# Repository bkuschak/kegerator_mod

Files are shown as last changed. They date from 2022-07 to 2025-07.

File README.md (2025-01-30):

# kegerator mod  

This project is a workaround to prevent short cycling on the Komos V2 kegerator. 

For some unknown reason the temperature controller occassionally turns the 
compressor on for about 1 second then immediately shuts it off. On my kegerator,
this can happen several times per hour. It tends to happen more often when the 
temperature setpoint is above 45 °F.

The workaround is to insert a small microcontroller board between the controlller
board and the compressor. This board intercepts the signal that controls the 
compressor. The software filters out any short transients and enforces a minimum 
on-time and a minimum off-time for the compressor.  

It has been running fine on my kegerator for several years now.

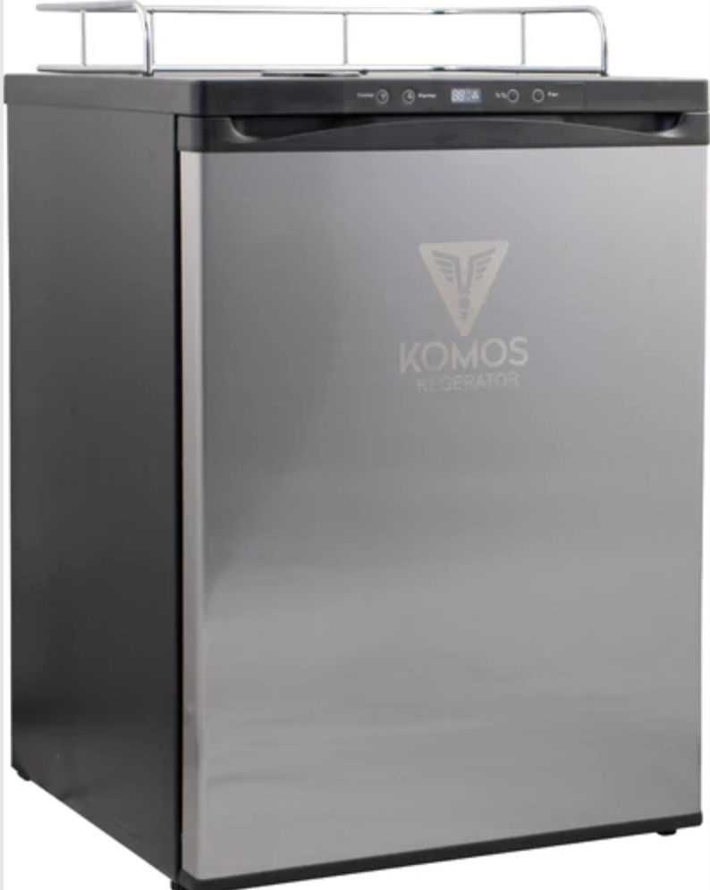
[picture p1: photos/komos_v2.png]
komos_v2


The board is installed inline between the front panel temperature controller and the 
compressor power board.

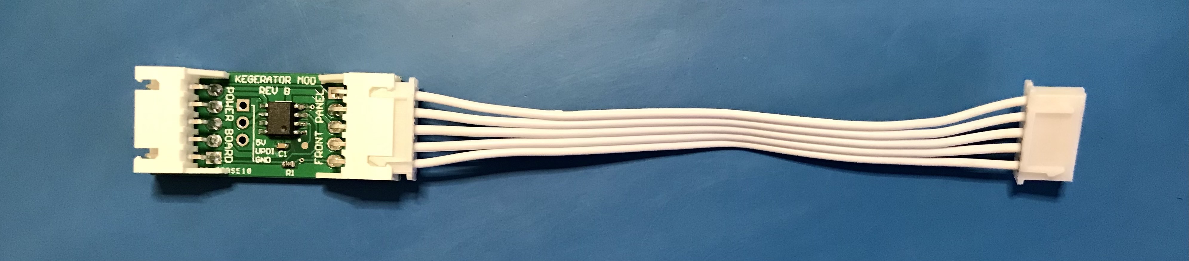
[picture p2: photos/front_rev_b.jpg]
front

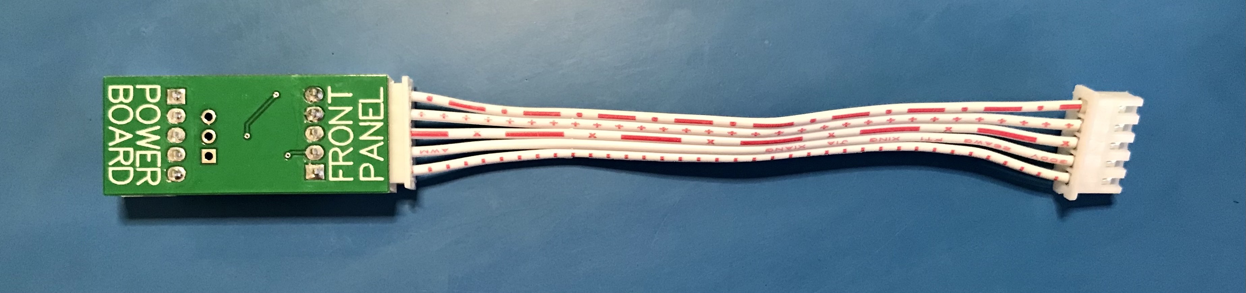
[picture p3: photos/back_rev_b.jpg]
back


See the other folders for more information on the [hardware](hardware/README.md) 
and [software](software/README.md).

If you need hardware, contact me.  I may still have a few boards in stock.

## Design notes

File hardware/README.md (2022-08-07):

## Hardware

Designed in Altium CircuitMaker.  Contact me if you want access to the project files in the Altium cloud.

Install R1 to allow the fan control to work normally. There's an option to have the software override the fan speed, but that is not implemented yet. If using this option then do not install R1.

### Installation

- Unplug the kegerator AC power.
- Remove the three screws that secure the plastic panel under the temperature controller front panel.
- Remove the two screws that secure the temperature controller front pabel assembly.
- Disconnect the 5 pin cable from the temperature controller.
- Insert the kegerator_mod PCBA inline as shown. Use the short cable to connect it to the front panel.
- The board connectors are labeled "Front Panel" and "Power Board".  Make sure the "Front Panel" side faces the temperature controller front panel.  "Power Board" side connects to the 5-pin cable that travels back into the kegerator.
- Reassemble in reverse order.  Bend the cable as needed to fit the space available.
- Reattach kegerator AC power.

The unit should function as normal, with the exception that compressor minimum on-time and minimum off-time are enforced. Short glitches are filtered out.

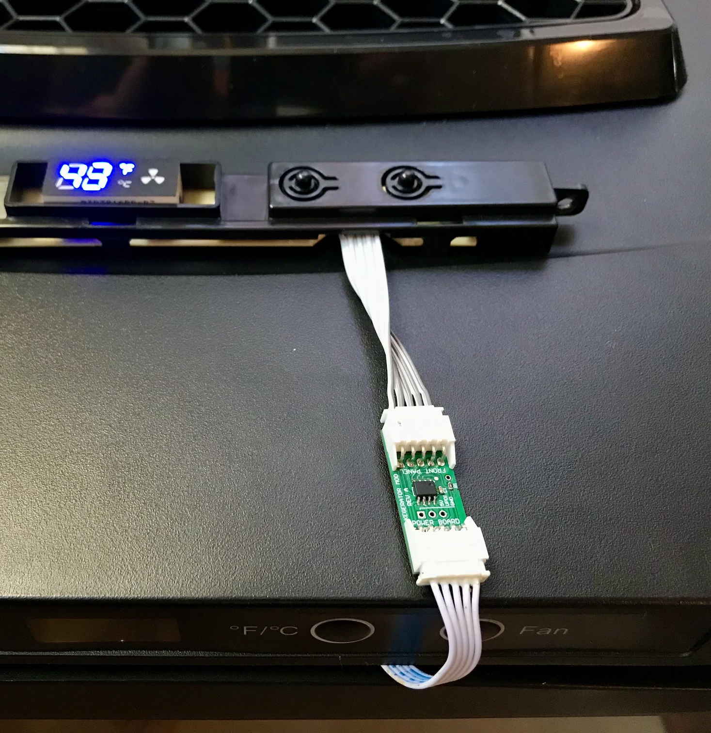
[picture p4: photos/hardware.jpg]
ppm_plot


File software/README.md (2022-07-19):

## Arduino sketch for ATTINY212

At the time of writing, the ATTINY212 is currently available at [Digikey](https://www.digikey.com/en/products/detail/microchip-technology/ATTINY212-SSN/9947536).

### Prerequisites

First, install these libraries:

```
https://github.com/SpenceKonde/megaTinyCore
https://github.com/contrem/arduino-timer
```

Configure as shown:

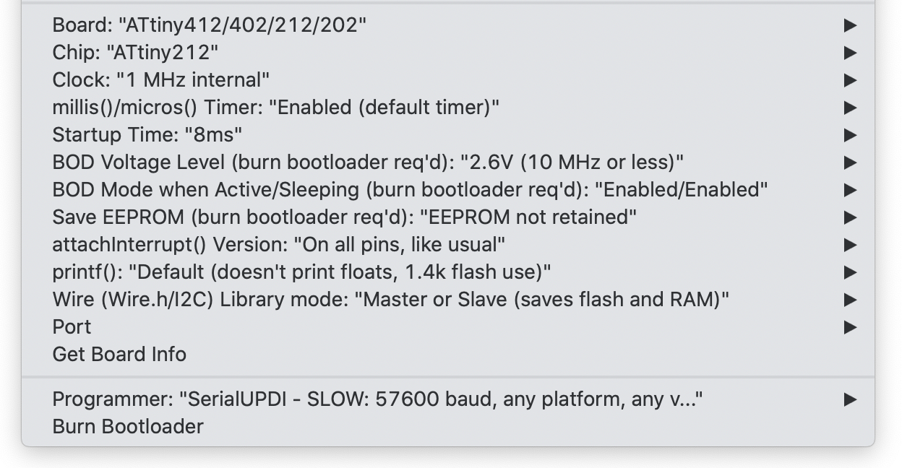
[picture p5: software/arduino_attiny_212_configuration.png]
configuration


### Programming

Programming can be done with a [UPDI programmer](https://www.amazon.com/dp/B09X64YRLD) and 3 jumper wires temporarily inserted into the board.

Burn the bootloader once to program the fuses. Then upload the sketch.

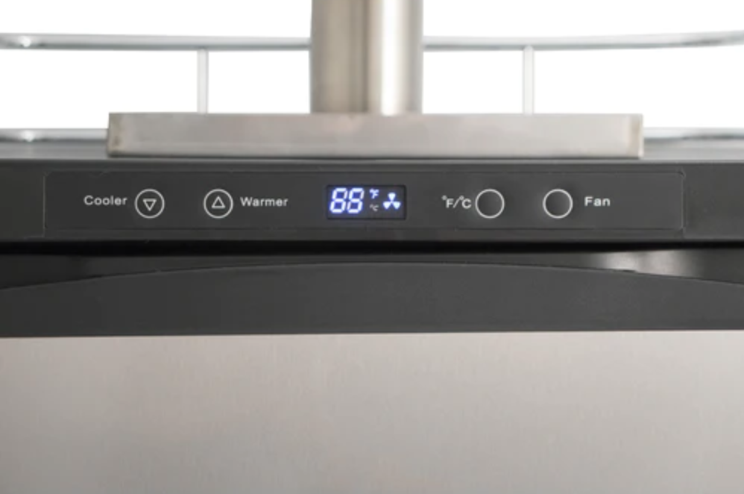
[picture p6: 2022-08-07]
photos/komos_v2_temperature_controller.png

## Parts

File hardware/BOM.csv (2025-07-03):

Quantity | DNS | Designator | Manufacturer | Manufacturer Part Number | Comment | Description | URL
1 |  | C1 | Taiyo Yuden | EMK107BJ104KAHT | 100 nF | Cap Ceramic 0.1uF 16V X5R 10% Pad SMD 0603 85°C Automotive T/R
1 | DNS | J1 | Amphenol | 68001-203HLF | Amphenol ICC / FCI 68001-203HLF | Conn Unshrouded Header HDR 3 POS 2.54mm Solder ST Top Entry Thru-Hole BergStik® Bulk
2 |  | J2, J3 | JST | JST S5B-XH-A(LF)(SN) | JST S5B-XH-A(LF)(SN) | HEADER, RIGHT ANGLE, 5WAY; Connector Type: Wire-to-Board; Gender: Pin; Ways, No. of: 5; Lead Spacing: 2.5mm; Terminat...
1 |  | R1 | Vishay Dale | CRCW06030000Z0EB | CRCW06030000Z0EB | Thick Film Resistors - SMD 1/10watt ZEROohm Jumper
1 |  | U1 | Microchip | ATTINY212-SSN | ATTINY212-SSN | Microcontroller with Core Independent Peripherals and picoPower Technology 8-Bit AVR RISC 2KB Flash 8-Pin SOIC
1 | DNS | J4 | Unknown | XH2.54-5pin 10cm | Ebay glhk05 | 5 Pin 2.54mm Pitch Female to Female JST-XH Connector Cable Wires | https://www.ebay.com/itm/194994928793?var=494877982672

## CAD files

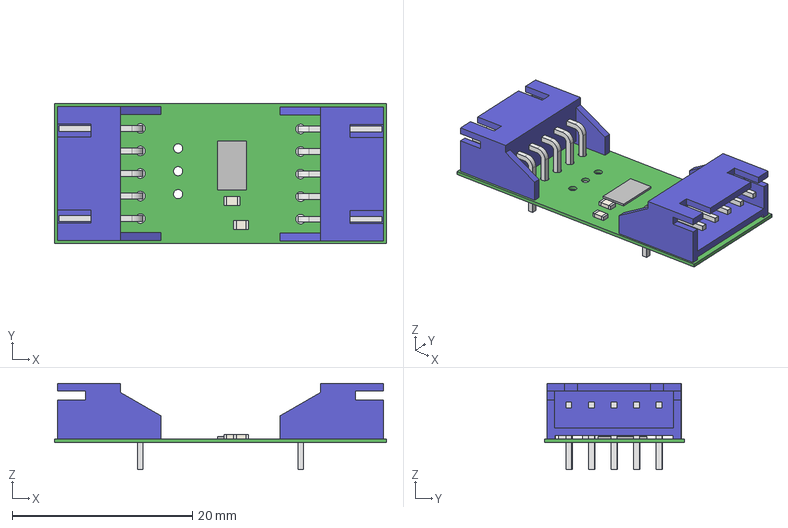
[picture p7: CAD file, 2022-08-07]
hardware/kegerator_mod_rev_b.step
36.8 x 15.5 x 9.55 mm
Extruded x 7
S5B-XH-A x 2

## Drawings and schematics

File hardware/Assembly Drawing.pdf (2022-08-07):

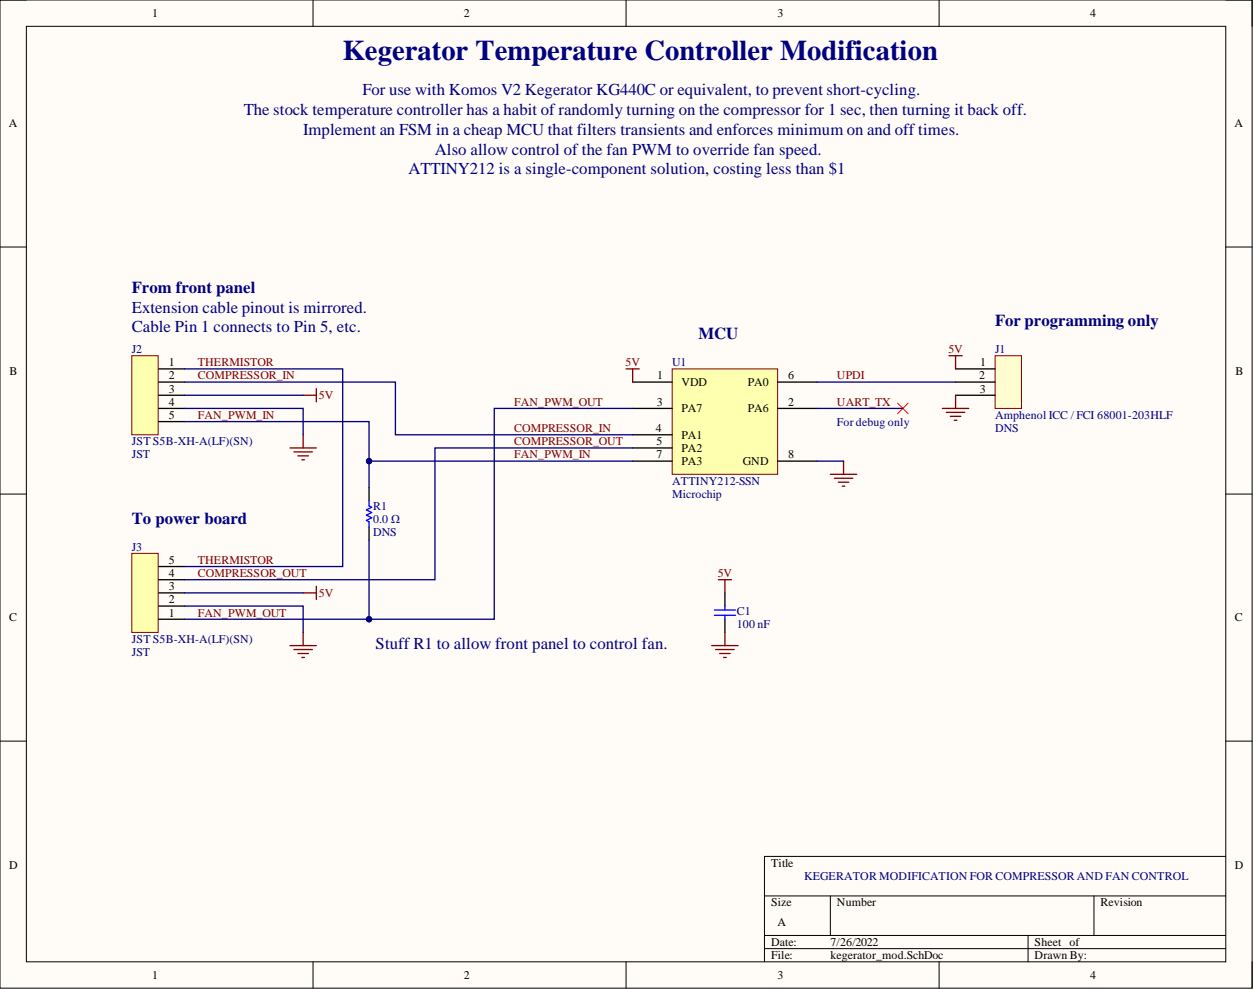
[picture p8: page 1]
N FOR COMPRESSOR; l ICC; / FCI; The stock; temperature control; ler has a habi; turning on; t back off.; in a cheap MCU; than $1; For programming onl; For use; G440C or equivalent; lso al; JST S5B-X; Stuff R1

Kegerator Temperature Controller Modification

t of random
that fi
the fan PWM

to prevent short-cycl

the compressor for 1 sec,

mplement an FSM

transients and enforces

mum on and off

low control of

to override fan speed.
ion, cost

is a single-component solut

From front panel
Extension cable pinout
Cable Pin 1 connects

to Pin 5, etc.

FA N _PWM_ O U T | 3

FA N _PWM_ IN | | 4

H-A(LF)(SN ) | COMPRESSOR_ O U T | 5

FA N _PWM_ IN | 7

To power board

low front panel

to control fan.

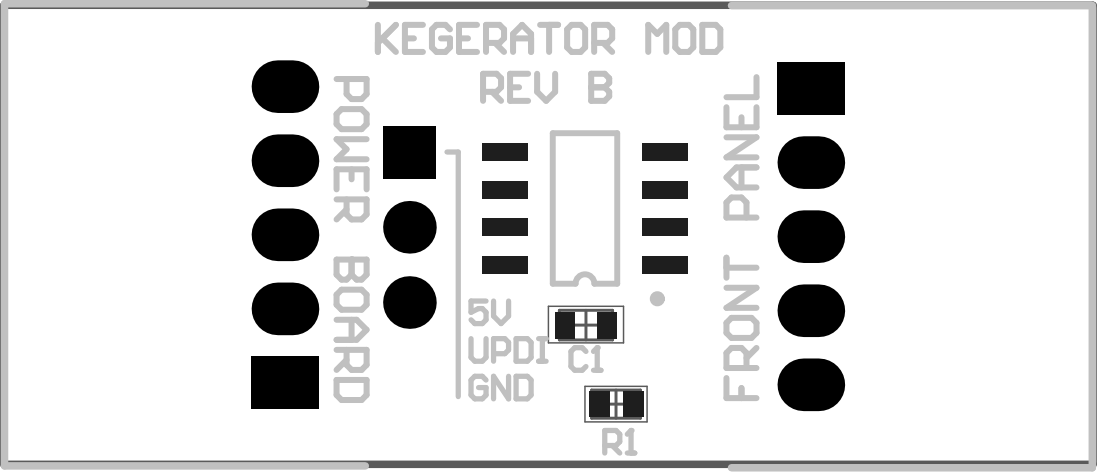
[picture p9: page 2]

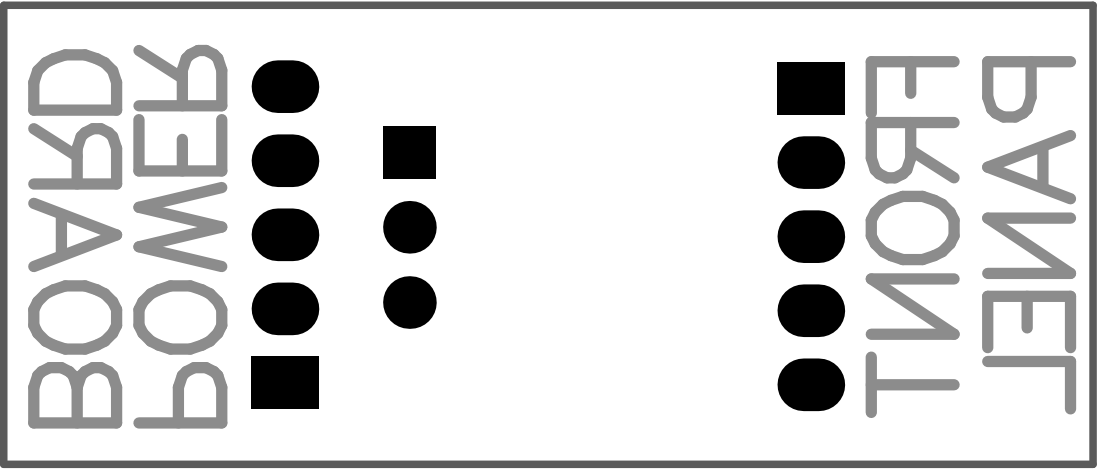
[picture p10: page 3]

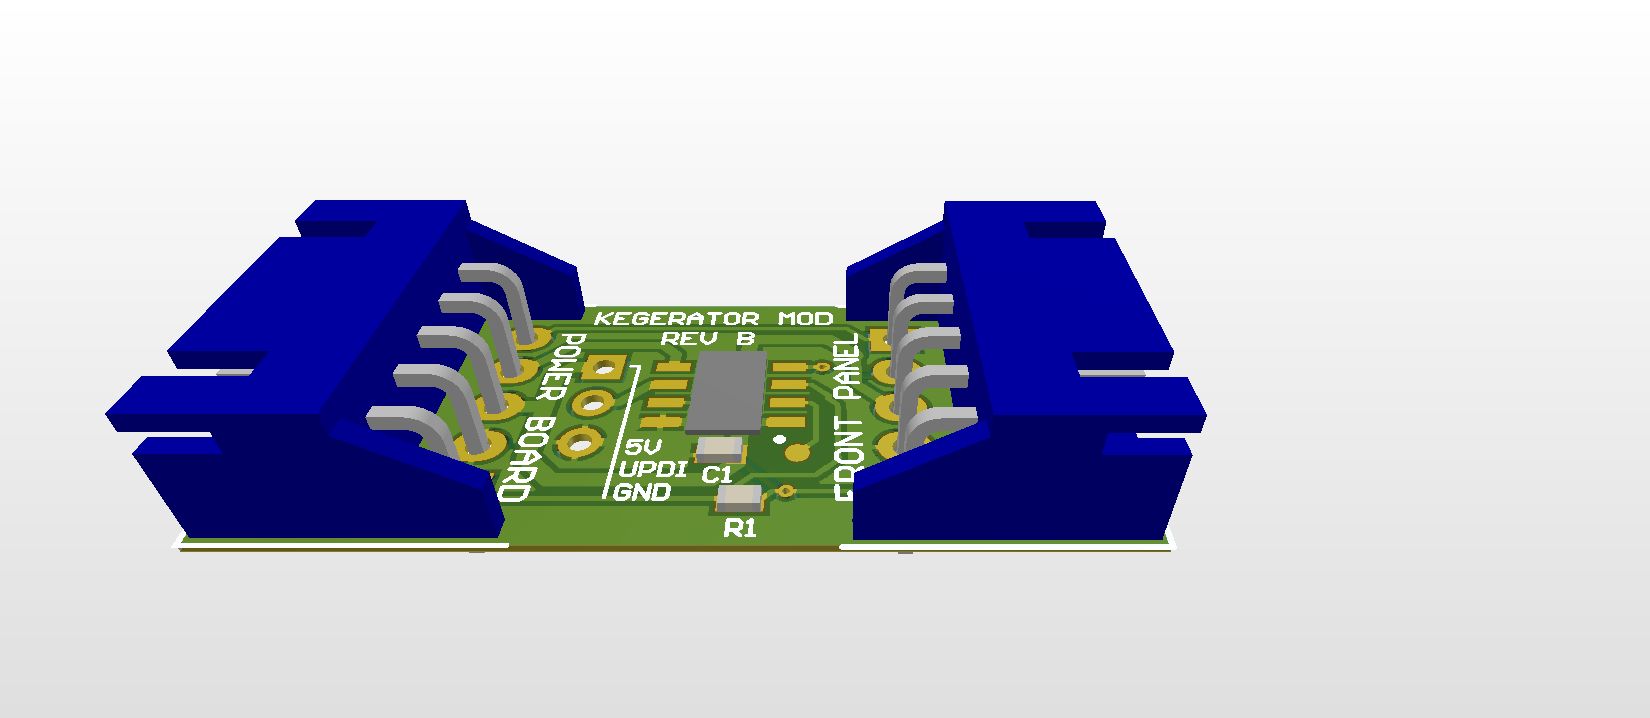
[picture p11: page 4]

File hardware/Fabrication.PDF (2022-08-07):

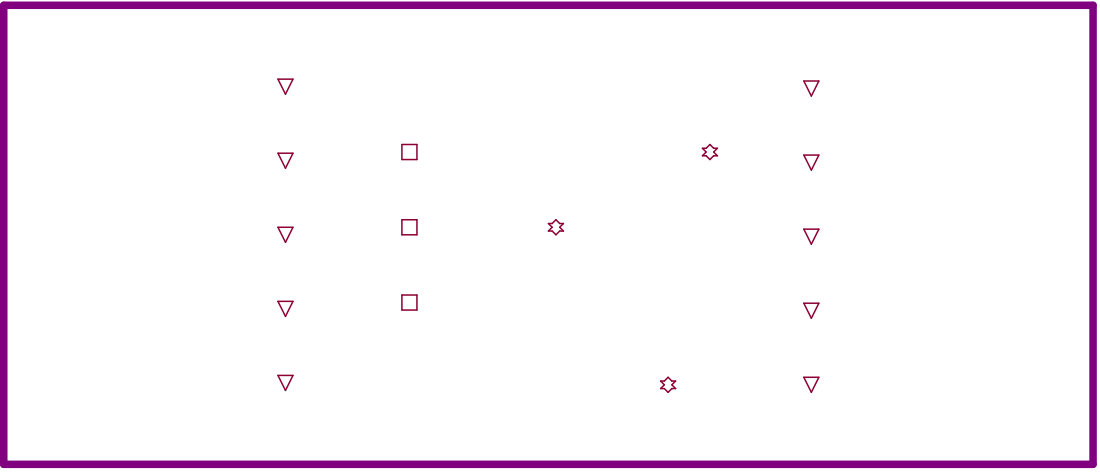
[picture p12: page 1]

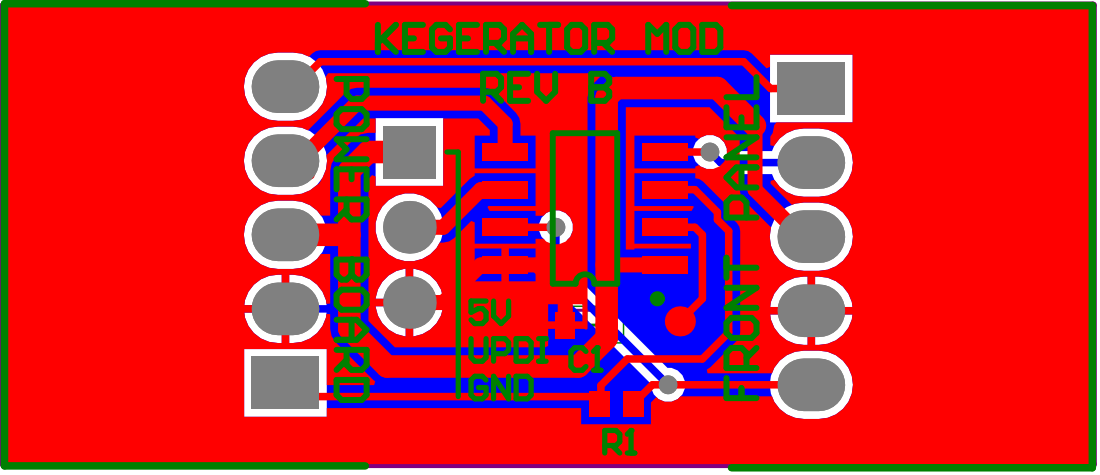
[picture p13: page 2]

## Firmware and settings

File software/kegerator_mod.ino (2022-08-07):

// Workaround to prevent short cycling on the Komos V2 kegerator.
// For some unknown reason the temperature controller randomly
// turns the compressor on for 1 second, then shuts it back off.
// This happens several times per hour. It tends to happen more
// often when the temperature setpoint is above 45 deg F.
// 
// This software implements a workaround using a small MCU inline
// on the compressor enable signal, to filter out these transients
// and enforce minimum on-time and minimum off-time for the 
// compressor.
//
// Device:
// ATTINY212 8-pin package.
// 5V operation. 1 MHz internal osc.
// ULPI programming using PA0.
// I/O using PA2, PA1.
// 
// https://github.com/bkuschak/kegerator_mod

#include <arduino-timer.h>

#define VERSION                 10   // Software version 1.0

#define COMPRESSOR_INPUT_PIN    2     // PA1 - pin 4
#define COMPRESSOR_OUTPUT_PIN   3     // PA2 - pin 5
#define FAN_PWM_OUTPUT_PIN      1     // PA7 - pin 3
#define FAN_PWM_INPUT_PIN       4     // PA3 - pin 7
#define DEBUG_PIN               0     // PA6 - pin 2

// If input is asserted for > 5 seconds then turn the output on.
#define ON_DELAY 5

// Once output is turned on, keep it on for at least 120 seconds.
#define MIN_ON_TIME 120

// If input is deasserted for > 5 seconds then goto OFF state.
#define OFF_DELAY 5

// Once output is turned off, keep it on for at least 120 seconds.
#define MIN_OFF_TIME 120

// TODO - 10 HZ PWM for fan on PA7 using TCD0/WOB. Using PA3 to detect FAN_PWM_IN

enum state_e { OFF = 0, ON } state;
uint16_t timeout;
uint16_t counter;
Timer<1> timer;   // msec timer resolution.

inline void compressor_on() {
  digitalWrite(COMPRESSOR_OUTPUT_PIN, HIGH);
}

inline void compressor_off() {
  digitalWrite(COMPRESSOR_OUTPUT_PIN, LOW);
}

// Call this function once per second, using the timer.
bool fsm(void* none) {

  // Toggle the debug pin.
  digitalWrite(DEBUG_PIN, !digitalRead(DEBUG_PIN)); 
  
  // Update timeout.
  if (timeout > 0)
    timeout--;

  switch (state) {
    case OFF:
      // Keep track of how long input has been continously asserted.
      if (digitalRead(COMPRESSOR_INPUT_PIN) == HIGH)
        counter++;
      else
        counter = 0;

      // Keep off for minimum amount of time.
      // Afterwards, turn on if the input has been continously
      // asserted for ON_DELAY seconds.
      if (timeout == 0) {
        if (counter >= ON_DELAY) {
          compressor_on();
          timeout = MIN_ON_TIME;
          counter = 0;
          state = ON;
        }
      }
      break;

    case ON:
      // Keep track of how long input has been continously deasserted.
      if (digitalRead(COMPRESSOR_INPUT_PIN) == LOW)
        counter++;
      else
        counter = 0;

      // Keep on for minimum amount of time.
      // Afterwards, turn off if the input has been continously
      // deasserted for OFF_DELAY seconds.
      if (timeout == 0) {
        if (counter >= OFF_DELAY) {
          compressor_off();
          counter = 0;
          timeout = MIN_OFF_TIME;
          state = OFF;
        }
      }
      break;
  }
  return true;    // run again next time
}

void setup() {
  pinMode(COMPRESSOR_INPUT_PIN, INPUT_PULLUP);
  pinMode(FAN_PWM_INPUT_PIN, INPUT);
  pinMode(FAN_PWM_OUTPUT_PIN, INPUT);   // Ignored for now.
  pinMode(DEBUG_PIN, OUTPUT);
  digitalWrite(COMPRESSOR_OUTPUT_PIN, LOW);
  pinMode(COMPRESSOR_OUTPUT_PIN, OUTPUT);
  digitalWrite(DEBUG_PIN, LOW);
  pinMode(DEBUG_PIN, OUTPUT);
  
  state = OFF;
  timeout = 0;
  counter = 0;

  // Run the FSM once per second.
  timer.every(1000, fsm);
}

void loop() {
  timer.tick();
}

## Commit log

2022-07-19 Add board files.
    [BOM.csv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]
2022-08-07 Remove Rev A files.
    [kegerator_mod_rev_a.GBL, kegerator_mod_rev_a.GBO, kegerator_mod_rev_a.GBP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]
2022-08-07 Add Rev B files.
    [BOM.csv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]
2022-09-22 Update BOM.csv
    Add cable to BOM.
    [BOM.csv]
2025-07-03 Update BOM.csv
    Install R1 by default to allow normal fan control.
    [BOM.csv]
2025-07-03 Update BOM.csv
    Add purchasing link for the cable, which is not easy to source.
    [BOM.csv]
